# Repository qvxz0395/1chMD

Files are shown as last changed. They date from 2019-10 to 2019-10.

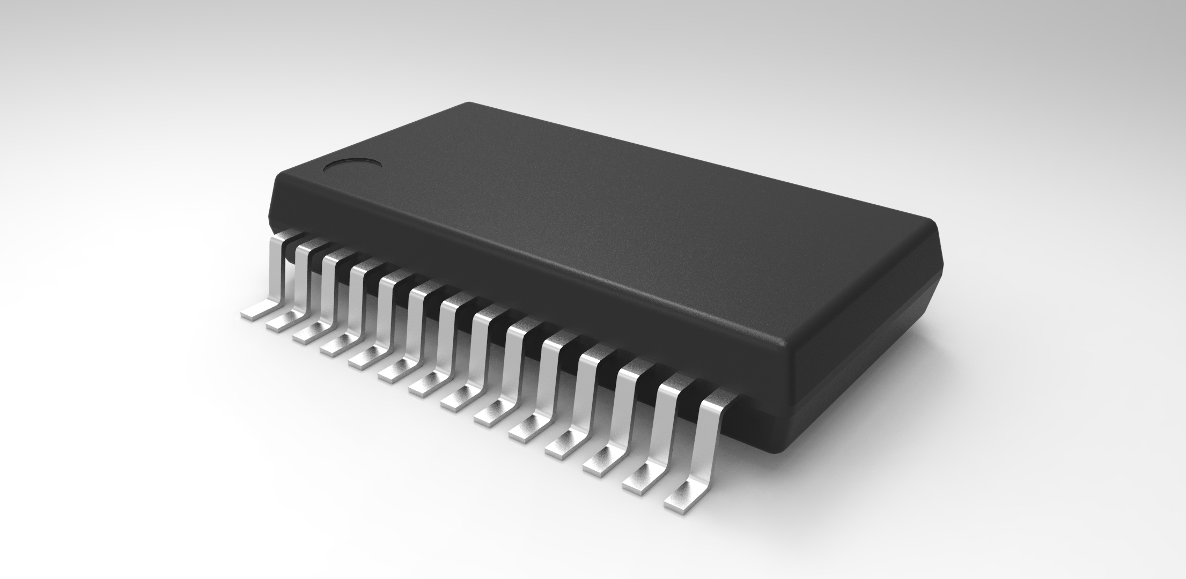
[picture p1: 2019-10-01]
1chMD_Circuit/Mylib/tssop-28-1.snapshot.1/untitled.255.jpg

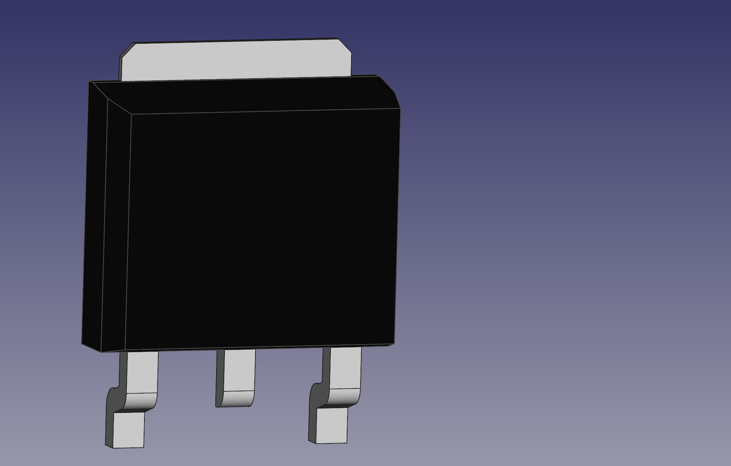
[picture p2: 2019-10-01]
1chMD_Circuit/Mylib/to252-1.snapshot.2/TO 252 Gehäuse.png

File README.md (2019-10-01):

# MD
## 要求仕様
  - 1ch
  - RZ735VA500W駆動可能
  - 出来ればPWM周波数50kHz(maxon motor controllerと同じ値)
  - 正転逆転
  - 電流制御
  - 速度制御
  - AMT102対応
  - CAN通信
  - 超小型,ターミナル方式

## 部品
  - メインマイコン
    - [STM32F042K6T6](http://akizukidenshi.com/catalog/g/gI-10789/)
    - [データシート](https://www.st.com/resource/en/datasheet/stm32f042c4.pdf) 
    - [リファレンスマニュアル](https://www.aps-web.jp/magazine/st/data/STM32F0x1_2_8RM_RM0091_JPN_rev1.pdf)

      - 250YEN
      - CAN 
      - 電流検出ADC12Bit
      - 書き込みデバッグ JTAG
      - ロータリーエンコーダ入力
      - とりあえず生やしとくピン
        - 4PDIPスイッチ
        - SPI1ch
        - USART1ch

  - CANトランシーバ
    - [ATA6561-GAQW-N](https://www.digikey.jp/product-detail/ja/microchip-technology/ATA6561-GAQW-N/ATA6561-GAQW-NCT-ND/9453180)
      - 63YEN
      - SOIC08
      - 電源 5V
      - 

  - 電流センサ
    - [ACS781KLRTR-150U-T](https://www.digikey.jp/product-detail/ja/allegro-microsystems-llc/ACS781KLRTR-150U-T/620-1851-1-ND/6677748)
      - 605YEN
      - ホール効果での電流検出
      - 検出可能電流 0~100[A] 過渡的に150[A], 17.6mV/A
      - 絶対最大定格 285[A],25℃
      - 

  - FET
    - [FDBL86561-F085](https://www.digikey.jp/product-detail/ja/on-semiconductor/FDBL86561-F085/FDBL86561-F085CT-ND/5209201)
      - 450 YEN @1
      - ドレインソース間電圧$V_{dss}$= 60[V]
      - ドレインソース間連続電流( $V_{gs}$ = 10[V], $T_c$ = 25[℃]) $I_D$= 300[A]
      - $I_d,V_{gs}$印加時の$R_{ds} On$= 1.1[mΩ] (max) @ 80[A] , 10[V]
      - $V_{gs}$印加時のゲート電荷 $Q_g$= 220[nC] (max) @10[V]
      - パッケージ　8-PowerSFN
    - 似た特性,同じパッケージのFET
      - [IPT007N06NATMA1](https://www.digikey.jp/product-detail/ja/infineon-technologies/IPT007N06NATMA1/IPT007N06NATMA1CT-ND/4571878)
      - [FDBL0110N60](https://www.digikey.jp/product-detail/ja/on-semiconductor/FDBL0110N60/FDBL0110N60CT-ND/5216101)

  - ゲートドライバ
    - [A3921KLPTR-T](http://akizukidenshi.com/catalog/g/gI-12293/)
      - 350YEN
      - フルブリッジMOSFETドライバ

  - 3.3Vレギュレータ
    - [NJM2845DL1-33](http://akizukidenshi.com/catalog/g/gI-11299/)
      - 50YEN
      - 最大入力電圧 14[V]
      - 出力電流　0.8[A]

  - 5Vレギュレータ
    - [NJM7805SDL1](http://akizukidenshi.com/catalog/g/gI-11237/)
      - 30YEN
      - 最大入力電圧 35[V]
      - 出力電流 1.5[A]

  - デジタルアイソレータ
    - [ADuM7440](https://www.digikey.jp/product-detail/ja/analog-devices-inc/ADUM7440ARQZ-RL7/ADUM7440ARQZ-RL7CT-ND/3897187)
      - 605YEN
      - 電源電圧 3-5.5[V]
      - 4Ch
      - データレート 1[Mbps]

  - モード変更用DIPSW
    - [EHS104LD](http://akizukidenshi.com/catalog/g/gP-05064/)

  - ショットキーバリアダイオード
    - 
## 計算(パワー回路設計)
  - [TeXコマンドをmarkdownでつかう方法](https://qiita.com/kgoto/items/2452b6dbaed5b3f7df78)

### ゲート抵抗
  - [参考](https://detail-infomation.com/gate-driver-gate-resistance-design/)

  FDBL86561-F085 のデータシートの表 Electrical Characteristics より
  
  Total Gate Charge $Q_g$ = 170[nC] (typ.) @ 10V 

  これより，

  ゲート駆動電圧 = 10[V]

  A3921KLPTR-T のデータシート表 ELECTRICAL CHARACTERISTICS Pulldown On Resistance 内の $I_{GHx} , I_{GLx}$より
  
  ゲート電流$I_G$= 150[mA]
  
  ゲート駆動回路の出力電圧$V_{OUT}= V_{REG} = 12.8[V]$より，(A3921の電気特性表より)

  ゲート抵抗$R_G$は

  $$ R_G = \dfrac{V_{out}}{I_G} = \dfrac{12.8[V]}{0.15[A]} = 85[Ω] $$

  ところで，
  電流iを時間tで積分したものが電荷$Q$なので，

  $$Q = \int idt$$

  ゲート電流$i_G$が時間$t_{ON}$流れることで，ゲートに蓄えられた電荷量が$Q_g$になる．

  $$Q_g = \int_0^{t_{ON}} I_G dt = I_G [t]_0^{t_{ON}} = I_G t_{ON}$$

  上記の関係より，

  $$ t_{ON} = \dfrac{Q_g}{t_{ON}} = \dfrac{170[nC]}{0.15[A]} = 1134[ns] $$

### デッドタイム

### チャージポンプコンデンサ

### ブートストラップコンデンサ

### 正逆転確認LEDの電流制限抵抗

### FFの電流制限抵抗

### 5V電源の電流制限抵抗

### 周波数

### 発熱

FETの発熱を考える．([参考](https://lab.fujiele.co.jp/articles/3129/))
他で発熱を考える必要があるのはゲートドライバICだけど，今回は無視．

損失は主に2種類ある．「オン抵抗と電流」によるものと「スイッチング損失」によるもの．

#### オン抵抗と電流

  $P = I^2R$

#### スイッチング損失

  FETはスイッチング時に損失が発生する．損失の式は．

  $ああああああ$

## マイコン関連

### ロータリーエンコーダ
  - [参考(STM32＋HALでエンコーダ―モード)](https://garberas.com/archives/244)

  - [参考(3.3V-5Vレベル変換)](http://kosakai.world.coocan.jp/change_3_3V_5V.html)

#### 回路
  よく使うインクリメンタルエンコーダ[AMT102](https://www.cui.com/product/resource/amt10.pdf)は電源$VDD=5$[V]駆動で,
  パルス信号出力も5[V]である．
  
  しかし，マイコンは3.3V駆動である．

  そのため，マイコンのピンの耐圧が5V以下だった場合，出力信号を[分圧](http://www.kairo-nyumon.com/resistor_divider.html)して電圧を落とさないといけない．

  マイコンの耐圧を確認する．今回の設計ではPA6とPB5,PB6が，エンコーダに接続されている．  
  データシートのP33からあるTable.13 pin definitionによると，それぞれのピンのI/O structureは順にTTa,FT,FTfである．  
  Table.12によると，TTaの耐圧が3.3V, FT,FTfの耐圧が5Vとなっている．また，Table18の絶対最大定格にはFT,FTfも内部プルアップ，プルダウンをすると**耐圧が下がる**と注3に書いてあるので，気を付ける．
  
  PA6だけは分圧必須である．（もう発注しちゃった，，，2019/08/21回路図及び配線図を修正）

#### プログラム

リファレンスマニュアルp341～にエンコーダインターフェースモードについての説明がある．

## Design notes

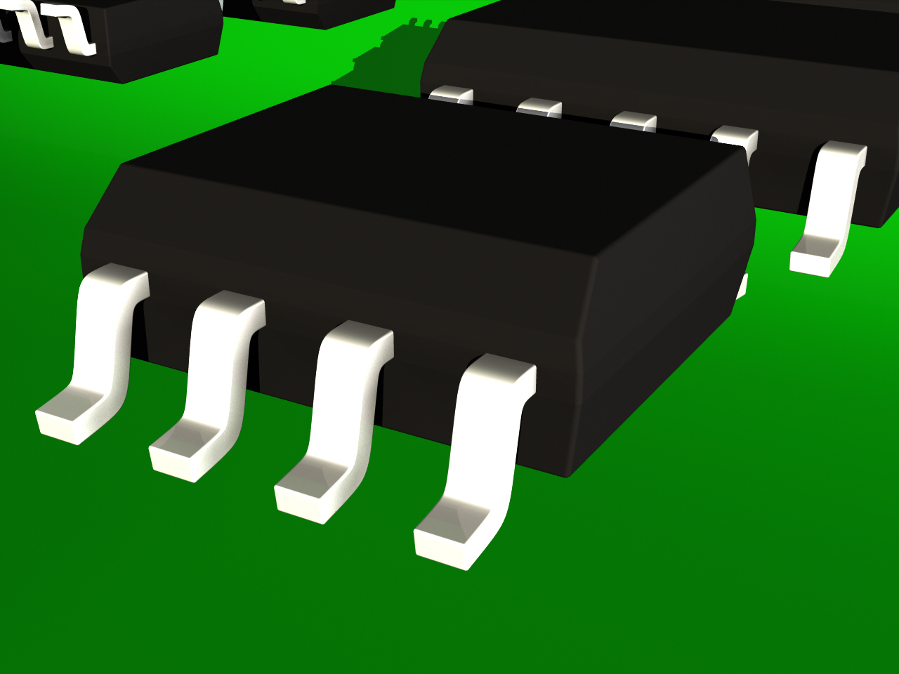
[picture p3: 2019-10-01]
1chMD_Circuit/Mylib/soic-package-narrow-8-10-14-and-16-pins-1.snapshot.3/SOIC narrow1.jpg

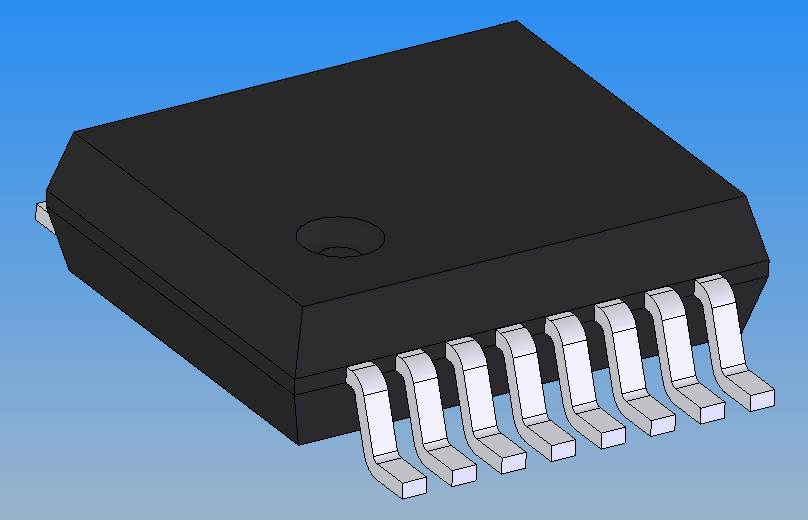
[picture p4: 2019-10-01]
1chMD_Circuit/Mylib/ssop16-2.snapshot.1/SSOP16.png

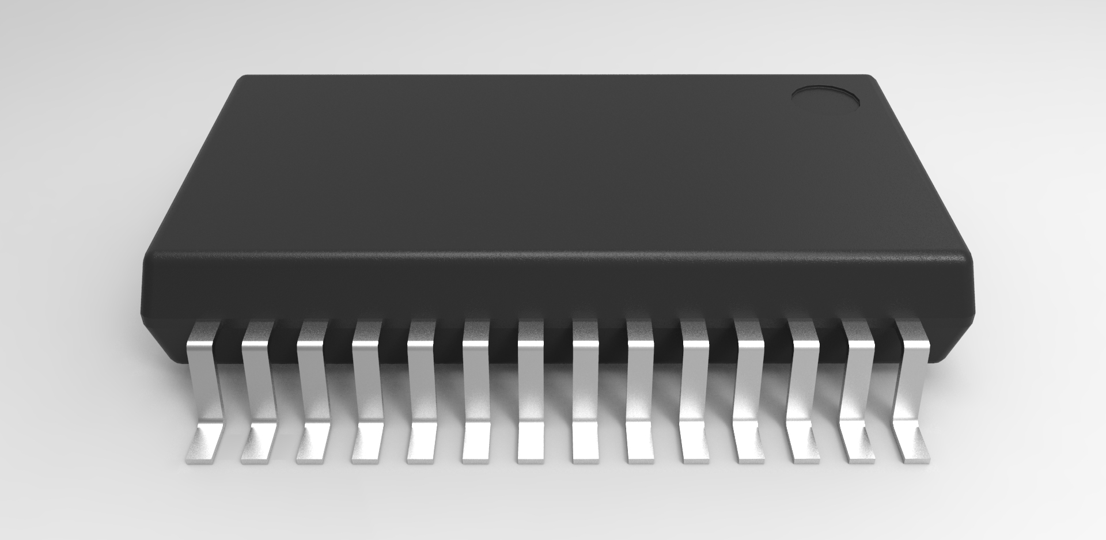
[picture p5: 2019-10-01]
1chMD_Circuit/Mylib/tssop-28-1.snapshot.1/untitled.256.jpg

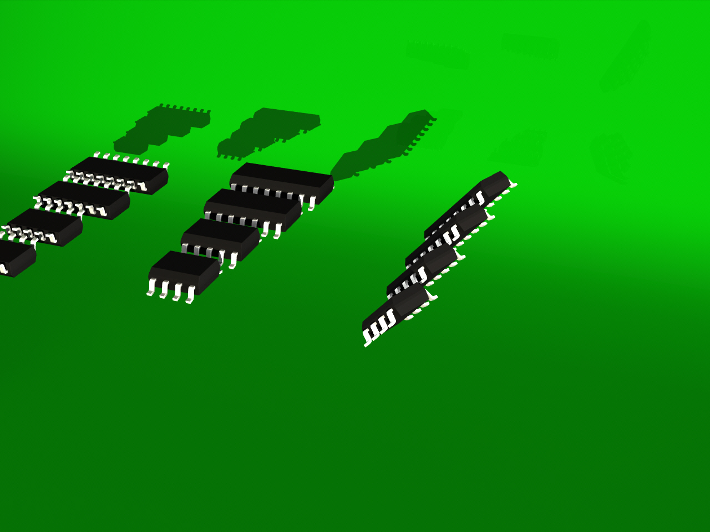
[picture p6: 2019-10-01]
1chMD_Circuit/Mylib/soic-package-narrow-8-10-14-and-16-pins-1.snapshot.3/SOIC narrow.jpg

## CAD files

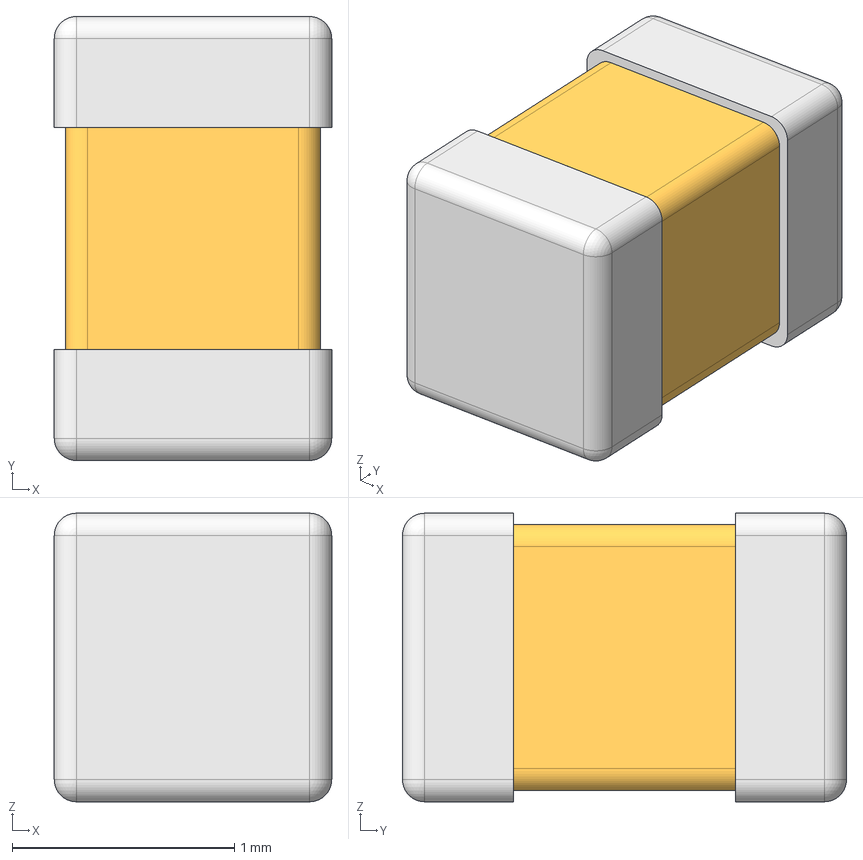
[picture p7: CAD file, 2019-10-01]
1chMD_Circuit/Mylib/models_3/models_3/capacitors/C0805.stp
1.25 x 2.00 x 1.30 mm

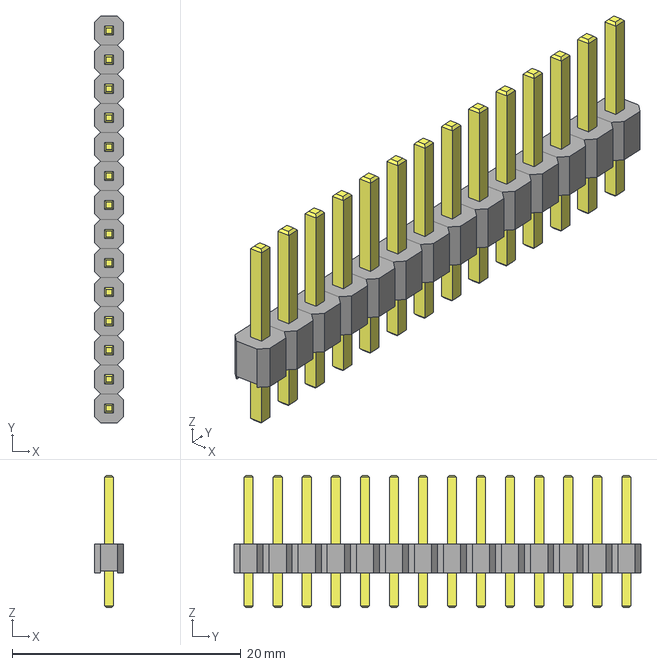
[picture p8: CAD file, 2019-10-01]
1chMD_Circuit/Mylib/models_3/models_3/connectors/goldpin/1x14.stp
2.54 x 35.6 x 11.5 mm

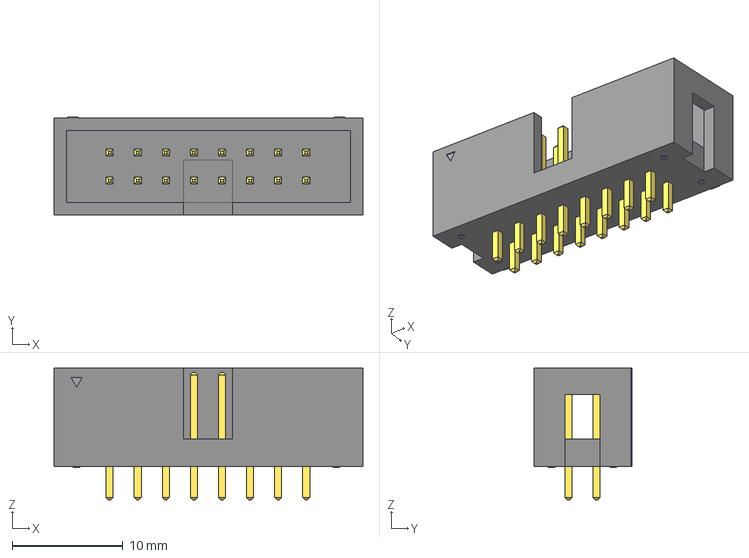
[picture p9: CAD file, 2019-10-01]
1chMD_Circuit/Mylib/models_3/models_3/connectors/ml/ml_16_v.stp
27.9 x 8.90 x 11.9 mm

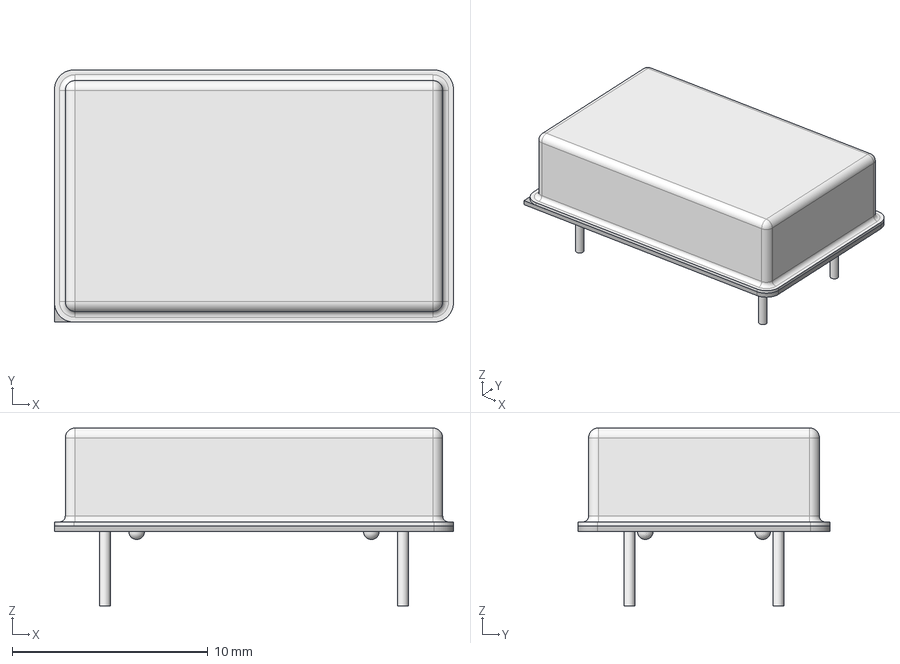
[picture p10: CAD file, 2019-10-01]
1chMD_Circuit/Mylib/models_3/models_3/crystals/DIL14S.stp
20.4 x 12.9 x 9.10 mm

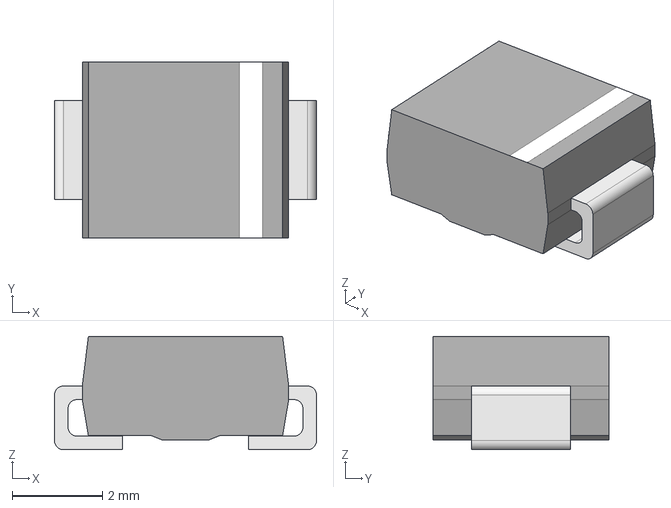
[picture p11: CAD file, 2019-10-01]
1chMD_Circuit/Mylib/models_3/models_3/diodes/SMB.stp
5.80 x 3.90 x 2.51 mm

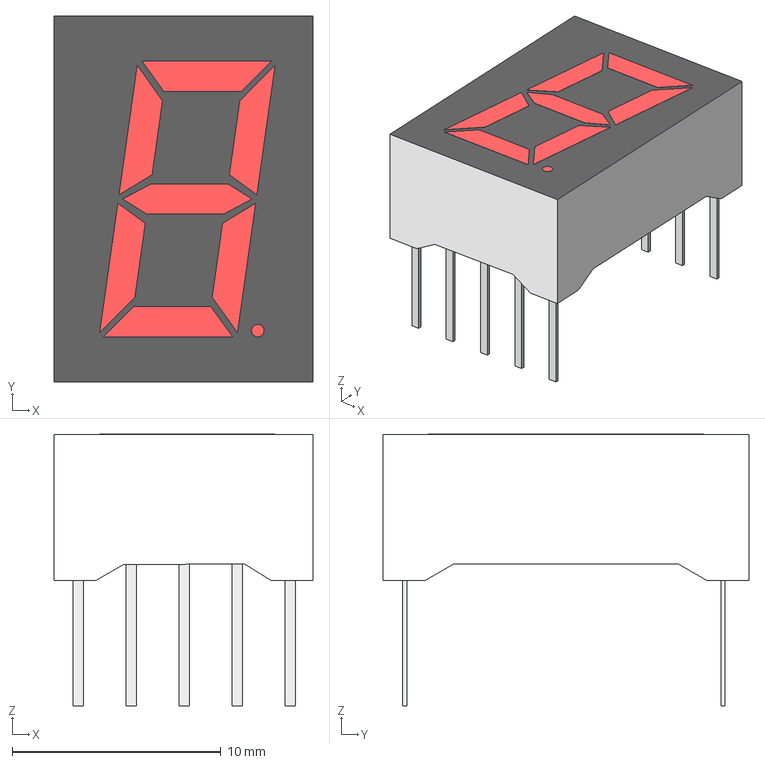
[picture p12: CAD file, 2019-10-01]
1chMD_Circuit/Mylib/models_3/models_3/display/7seg/size_13_2/x1_12x17.stp
12.4 x 17.5 x 13.0 mm

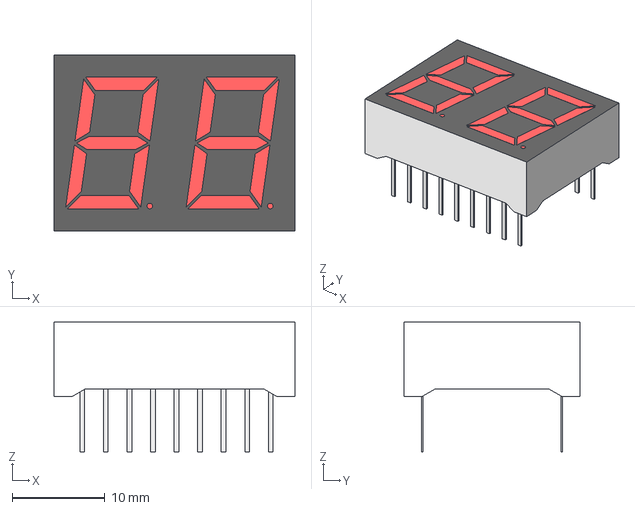
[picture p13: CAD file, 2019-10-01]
1chMD_Circuit/Mylib/models_3/models_3/display/7seg/size_14/x2_26x19.stp
26.0 x 19.0 x 14.0 mm

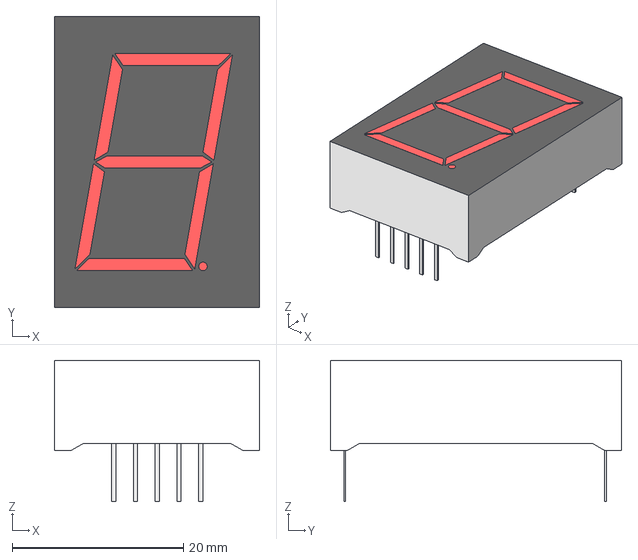
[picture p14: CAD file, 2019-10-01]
1chMD_Circuit/Mylib/models_3/models_3/display/7seg/size_25_4/x1_24x34.stp
24.0 x 34.0 x 16.5 mm

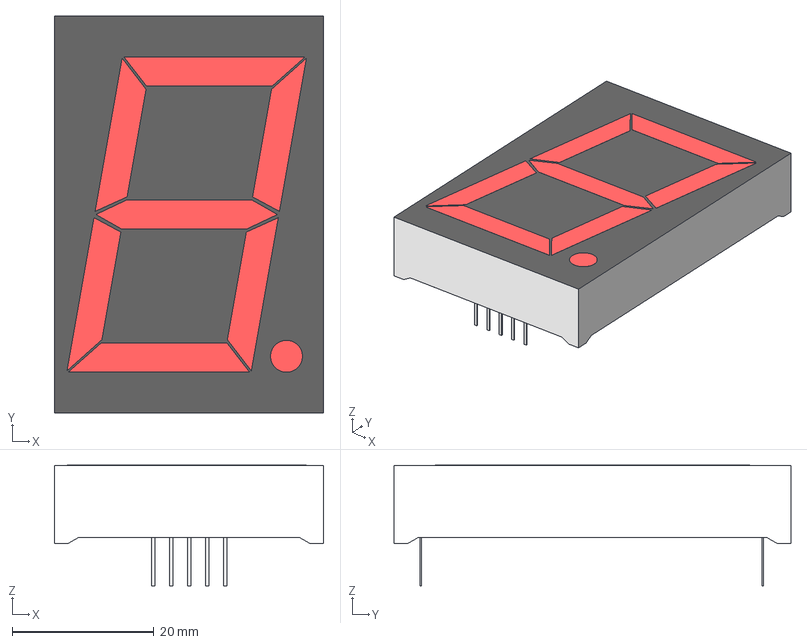
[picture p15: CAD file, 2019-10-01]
1chMD_Circuit/Mylib/models_3/models_3/display/7seg/size_44_5/x1_38x56.stp
38.0 x 56.0 x 17.0 mm

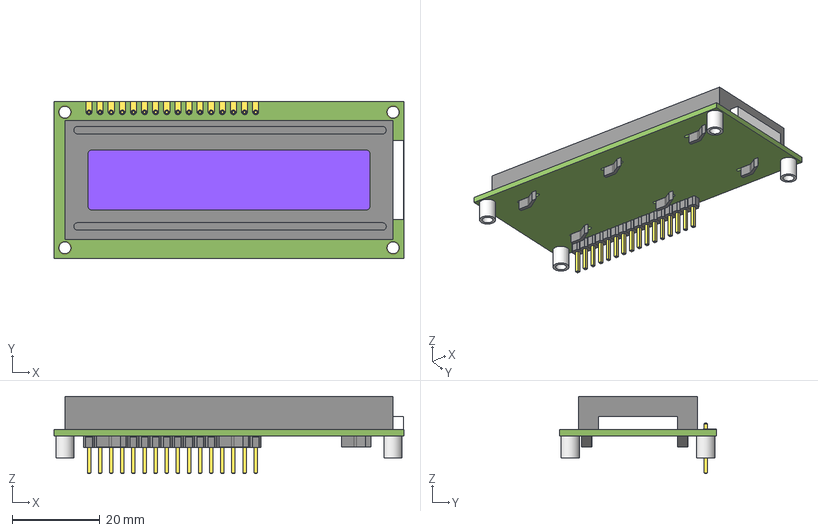
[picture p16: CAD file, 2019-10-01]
1chMD_Circuit/Mylib/models_3/models_3/display/lcd/lcd_16x2.stp
80.0 x 36.0 x 17.6 mm

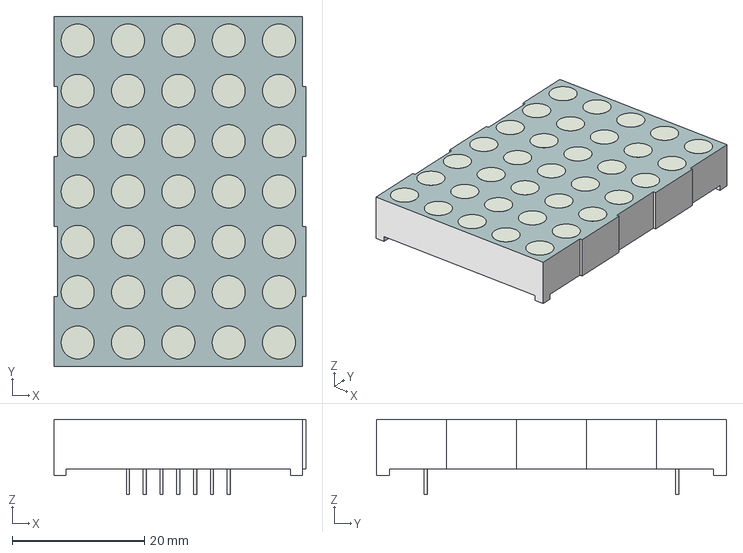
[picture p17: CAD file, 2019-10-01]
1chMD_Circuit/Mylib/models_3/models_3/display/matrix/50x37_5x7.stp
38.1 x 53.0 x 11.4 mm

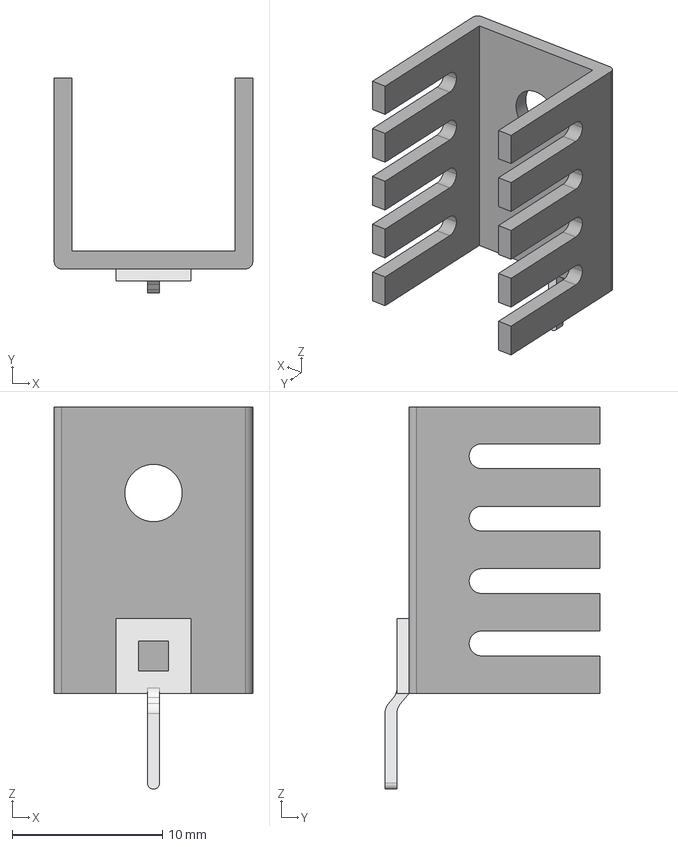
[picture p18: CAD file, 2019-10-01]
1chMD_Circuit/Mylib/models_3/models_3/heatsinks/D03PA.stp
13.2 x 14.3 x 25.4 mm

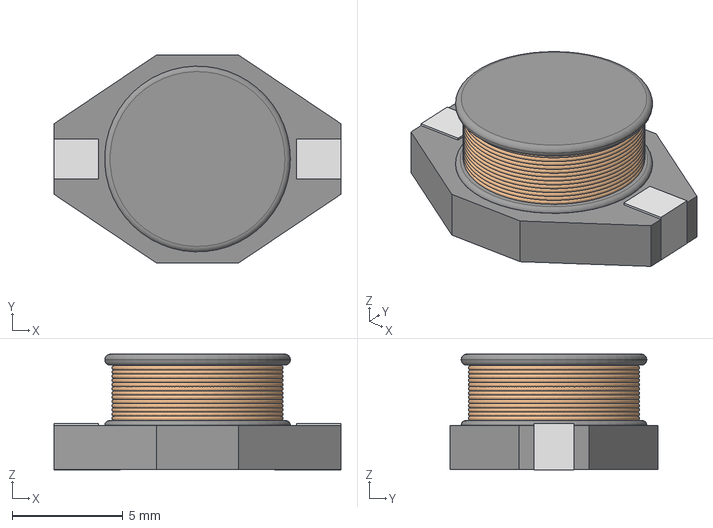
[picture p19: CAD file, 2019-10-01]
1chMD_Circuit/Mylib/models_3/models_3/inductor/DO3316P.stp
12.9 x 9.40 x 5.22 mm

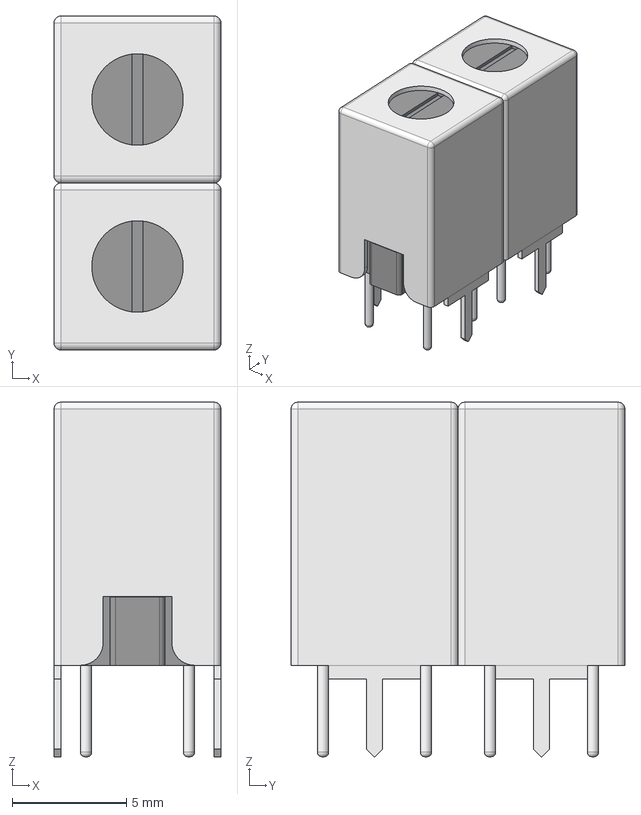
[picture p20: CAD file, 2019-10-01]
1chMD_Circuit/Mylib/models_3/models_3/inductor/neosid/71EX2RM225.stp
7.30 x 14.6 x 15.5 mm

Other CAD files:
1chMD_Circuit/Mylib/models_3/models_3/led/10mm.stp
1chMD_Circuit/Mylib/models_3/models_3/packages/bga/R_XBGA_N5.stp
1chMD_Circuit/Mylib/models_3/models_3/rectifiers/2KBB.stp
1chMD_Circuit/Mylib/models_3/models_3/resistors/R3020.stp
1chMD_Circuit/Mylib/LIB_EHS104LD/EHS104LD/Allegro/ehs104ld.psm
1chMD_Circuit/Mylib/LIB_EHS104LD/EHS104LD/DEHDL/ehs104ld/chips/chips.prt
1chMD_Circuit/Mylib/User Library-7-Pin PSOF Package.step
1chMD_Circuit/Mylib/User Library-PG-HSOF-8-1.step
1chMD_Circuit/Mylib/User Library-QFP32/User Library-QFP32.STEP
1chMD_Circuit/Mylib/User Library-QSOP16-1.step
1chMD_Circuit/Mylib/XT60 PLUG.STEP
1chMD_Circuit/Mylib/models_3/models_3/capacitors/C0201.stp
1chMD_Circuit/Mylib/models_3/models_3/capacitors/C0402.stp
1chMD_Circuit/Mylib/models_3/models_3/capacitors/C0504.stp
1chMD_Circuit/Mylib/models_3/models_3/capacitors/C0603.stp
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
